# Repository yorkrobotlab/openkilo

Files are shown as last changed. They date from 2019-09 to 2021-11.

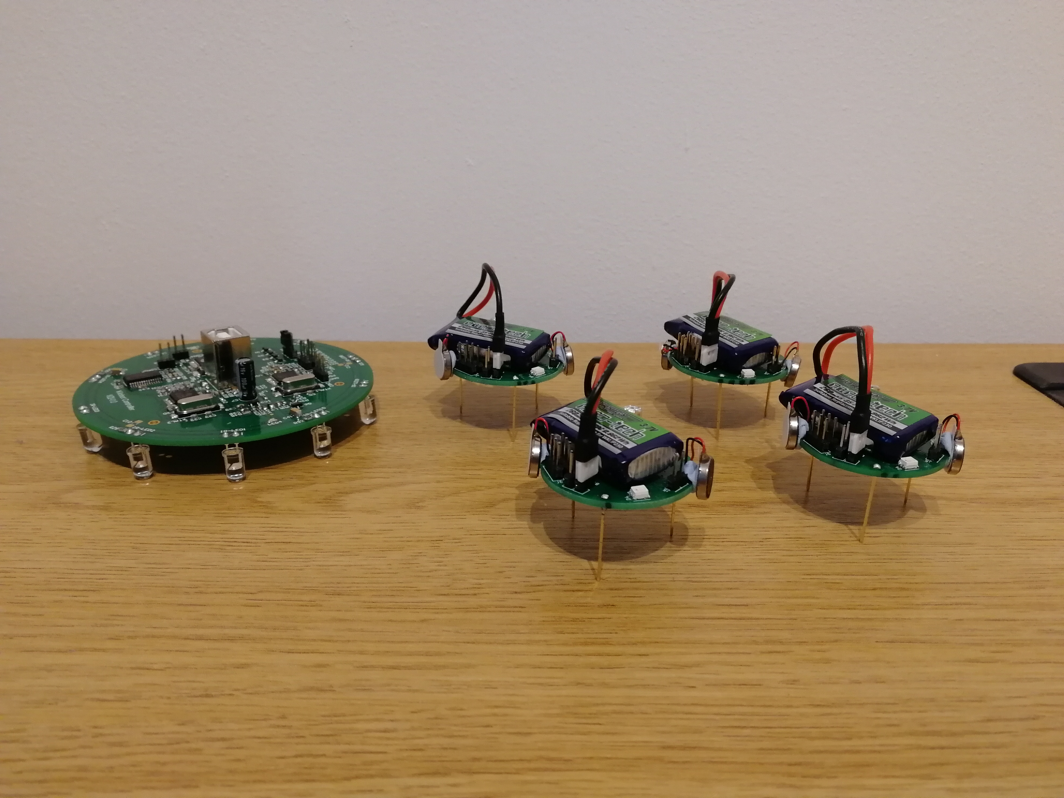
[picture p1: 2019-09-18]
Photos and Video/with_OHC.jpg

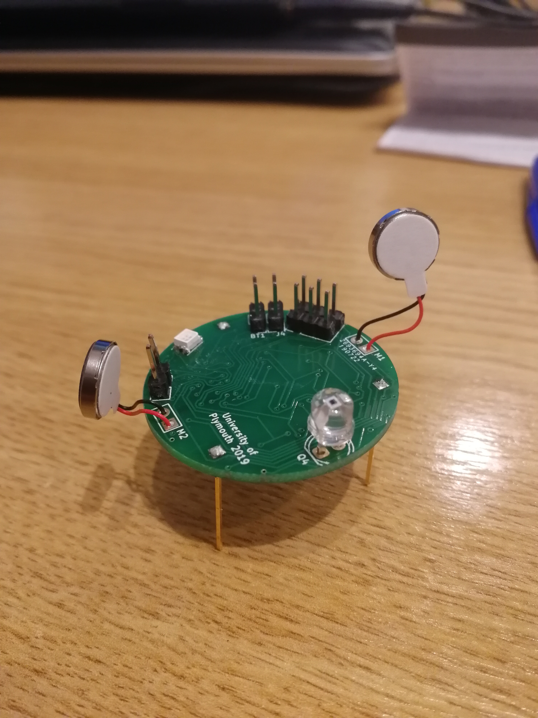
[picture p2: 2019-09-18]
Photos and Video/without_battery.jpg

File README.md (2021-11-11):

# OpenKilo

This repository contains resources related to the OpenKilo Kilobot revision, which was designed to aid repair and extensibility of the Kilobot platform.

This project was possible due to the material made open-source by other institutions, most importantly [Harvard University](https://ssr.seas.harvard.edu/kilobots) and [Western Carolina University](https://kilobot.wcu.edu/).

## Contents

* [Hardware Design](Hardware%20Design/) - KiCad project and exported Gerber files used to produce this version of the Kilobot
* [Documentation](Documentation/) - hardware schematic (produced from Harvard and WCU designs), assembly and programming guides, and bill of materials
* [Photos and Video](Photos%20and%20Video/) - showing the completed robots and their usage

## Requirements

Our Overhead Controller (OHC) was built to a design by Western Carolina University (WCU). Their detailed guide was also used for the programming and control of both the OHC and Kilobots. For more details, refer to their material at https://kilobot.wcu.edu/.

In particular:

* OHC Gerber files
* Software folder including Kilobot and OHC firmware
* [KiloGUI](https://github.com/acornejo/kilogui), GUI application for Kilobot control
* [Maker: A Kilobot Swarm](https://www.asee.org/public/conferences/64/papers/15441/view)

### Editing the PCB
[KiCad EDA](http://kicad.org/) is a free open-source electronic CAD suite which was used to create the OpenKilo design. KiCad is required in order to make changes to the design, but the exported Gerber files are also available for use directly.

The included Kilobot.lib is required for certain symbols and footprints, and must be added to the KiCad project using the process described [here](https://forum.kicad.info/t/library-management-in-kicad-version-5/14636).

[freeRouting](https://freerouting.org/) was used in conjunction with KiCad to carry out automatic PCB routing for the current design.

## Build Process
1. Purchase all PCBs and required components using BOMs included here. For the OHC PCB, use WCU Gerber files.

2. Following the guide in [Maker: A Kilobot Swarm](https://www.asee.org/public/conferences/64/papers/15441/view), install the required software before assembling the OHC and programming its firmware.

3. Assemble the OpenKilo hardware using the included assembly diagram and checklists.

4. Continuing with the WCU guide, program Kilobot firmware using a 2x3 header cable. Connection details are given in [Programming Reference.pdf](Documentation/Programming%20Reference.pdf).

5. Install KiloGUI and use the OHC to program a benchmark test onto the OpenKilo robots. These tests can be found in the WCU materials as well as at [Kilobotics](https://www.kilobotics.com/labs) where details of their functions are available.

## Author
The main OpenKilo design and prototyping was completed by Jamie Trump while a postgraduate student in the [School of Engineering, Computing and Mathematics](https://www.plymouth.ac.uk/schools/school-of-engineering-computing-and-mathematics) at the [University of Plymouth](https://www.plymouth.ac.uk/).

His original project repository can be found at [github.com/jamie-trump/Plymouth-Kilobot-2019](https://github.com/jamie-trump/Plymouth-Kilobot-2019).

This work is licensed under a [Creative Commons Attribution-NonCommercial-ShareAlike 4.0 International License](http://creativecommons.org/licenses/by-nc-sa/4.0/).

## Links

### Information and Publications
* [Kilobot @ WCU](https://kilobot.wcu.edu/)
* [Maker: A Kilobot Swarm](https://www.asee.org/public/conferences/64/papers/15441/view)
* [Kilobotics Labs](https://www.kilobotics.com/labs)

### Software
* [KiloGUI](https://github.com/acornejo/kilogui)
* [KiCad EDA](http://kicad.org/)
* [freeRouting](https://freerouting.org/)

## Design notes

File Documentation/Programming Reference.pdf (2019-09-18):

## Kilobot firmware programming connections

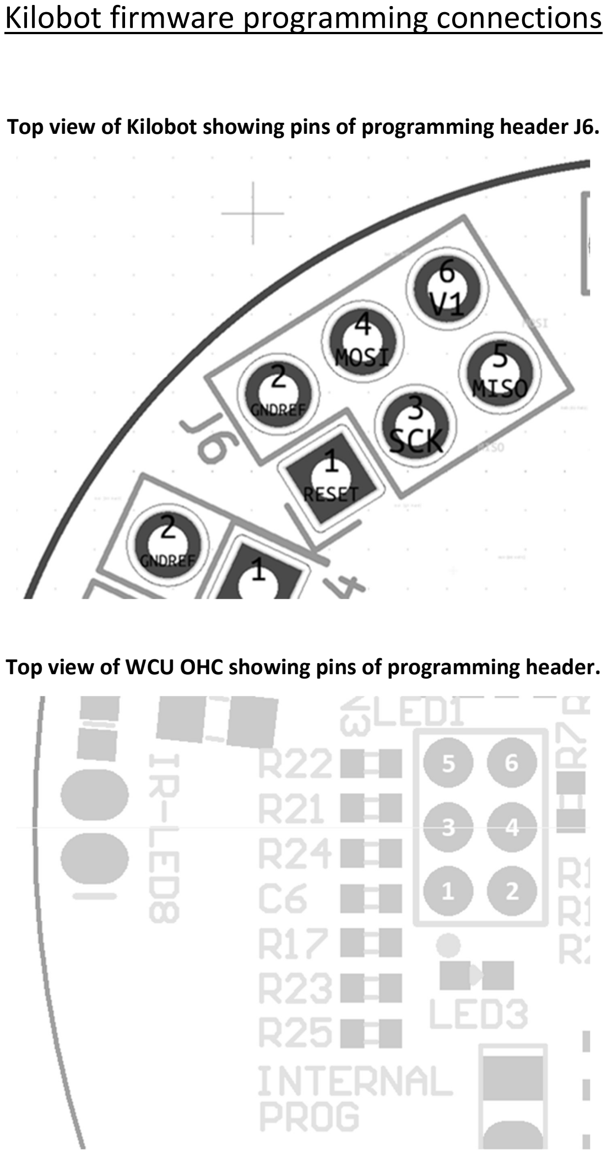
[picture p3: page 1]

Top view of Kilobot showing pins of programming header J6.

Top view of WCU OHC showing pins of programming header.

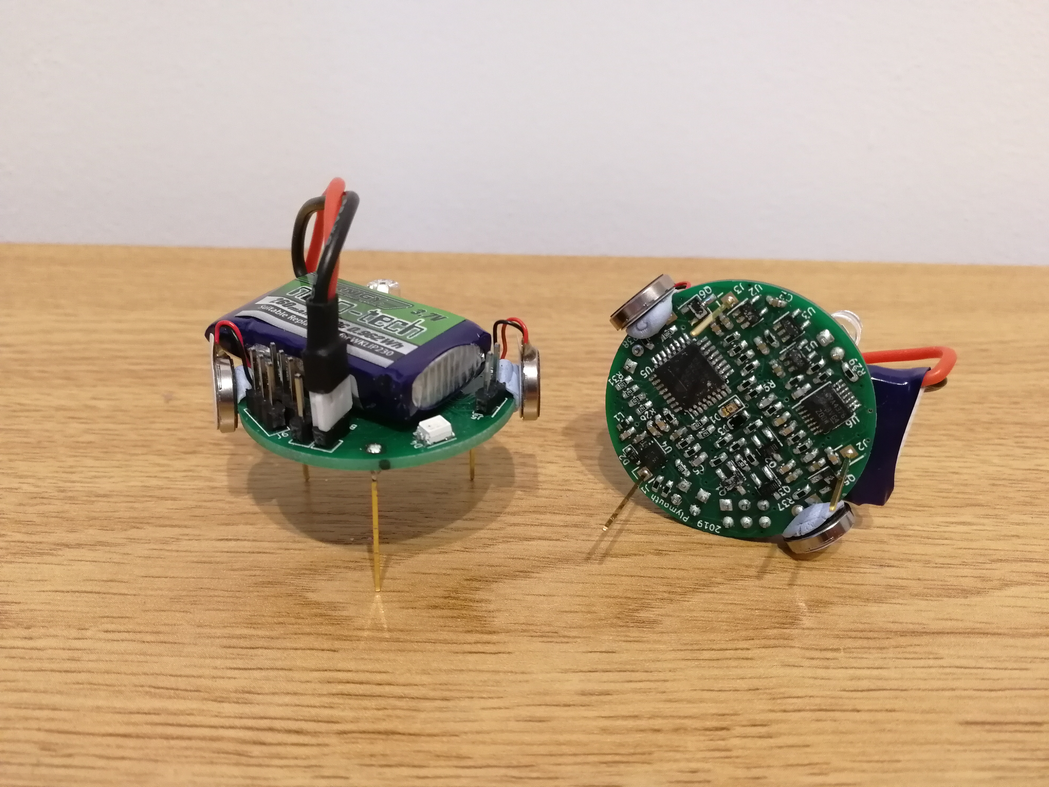
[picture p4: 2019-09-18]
Photos and Video/kilobots1.jpg

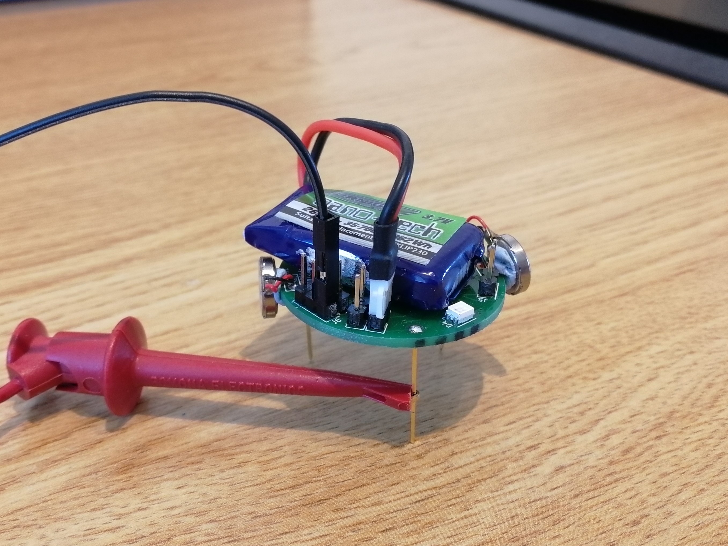
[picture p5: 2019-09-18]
Photos and Video/charging.jpg

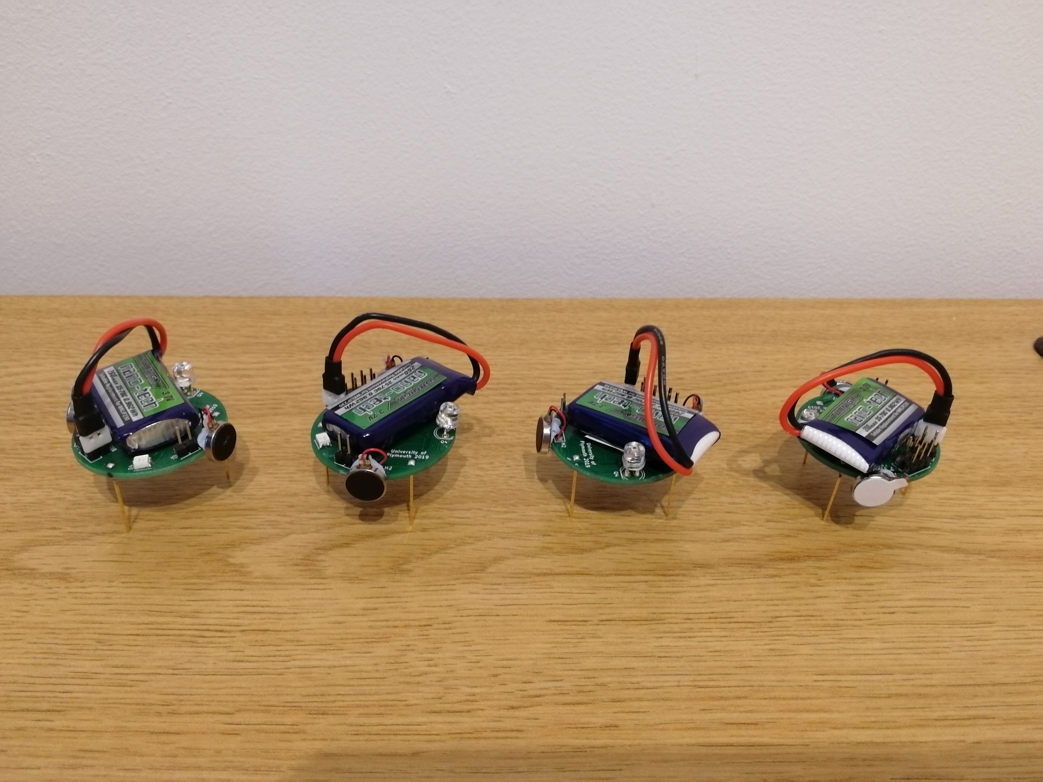
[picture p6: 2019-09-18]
Photos and Video/kilobots2.jpg

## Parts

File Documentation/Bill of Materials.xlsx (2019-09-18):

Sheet: 5x Kilobots
MyRef | Ordered Qty | Description | Supplier | Order Code | Price each (@qty), £ ex vat | Total (@qty), £ ex vat
1 | 50 | CAP CER 2.2UF 6.3V Y5V 0603 | Farnell | 2627450 | 0.0985 | 4.925
2 | 25 | CAP CER 10000PF 25V 10% X7R 0603 | Farnell | 1856354 | 0.0337 | 0.843
3 | 10 | CAP CER 0.1UF 16V 10% X7R 0603 | Farnell | 1327679 | 0.1020 | 1.020
4 | 10 | CAP CER 1000PF 50V 5% NP0 0603 | Farnell | 8819920 | 0.0700 | 0.700
5 | 5 | CAP CER 10000PF 25V 5% C0G 0603 | Digikey | 1276-2172-1-ND | 0.2700 | 1.350
6 | 10 | CAP CER 68PF 50V 5% C0G 0603 | Farnell | 1907295 | 0.1410 | 1.410
7 | 5 | IC CHARGER LI-ION USB/AC 10WSON | Digikey | LM3658SD-A/NOPBCT-ND | 1.0600 | 5.300
8 | 5 | DIODE SCHOTTKY 30V 100MA 0603 | Digikey | 641-1282-1-ND | 0.3500 | 1.750
9 | 10 | FIXED IND 10UH 50MA 900 MOHM | Farnell | 2840127 | 0.1080 | 1.080
10 | 5 | IC OPAMP GP 5.5MHZ RRO 14TSSOP | Digikey | 296-22565-1-ND | 2.6500 | 13.250
11 | 10 | RES SMD 0.82 OHM 1% 1/10W 0603 | Farnell | 1717771 | 0.0717 | 0.717
12 | 10 | RES SMD 1.18K OHM 1% 1/10W 0603 | Farnell | 2303149 | 0.0374 | 0.374
13 | 5 | RES SMD 1.47K OHM 1% 1/10W 0603 | Digikey | P1.47KHCT-ND | 0.0800 | 0.400
14 | 15 | RES SMD 1.6K OHM 5% 1/10W 0603 | Digikey | P1.6KGCT-ND | 0.0340 | 0.510
15 | 5 | RES SMD 1.62K OHM 1% 1/10W 0603 | Digikey | P1.62KHCT-ND | 0.0800 | 0.400
16 | 20 | RES SMD 10K OHM 1% 1/10W 0603 | Farnell | 2303192 | 0.0374 | 0.748
17 | 10 | RES SMD 10 OHM 1% 1/10W 0603 | Farnell | 2302958 | 0.0374 | 0.374
18 | 10 | RES SMD 11K OHM 1% 1/10W 0603 | Farnell | 2059409 | 0.0374 | 0.374
19 | 10 | RES SMD 154 OHM 1% 1/10W 0603 | Farnell | 2303077 | 0.0329 | 0.329
20 | 10 | RES SMD 2M OHM 5% 1/10W 0603 | Farnell | 2059687 | 0.0227 | 0.227
21 | 10 | RES SMD 2.26K OHM 1% 1/10W 0603 | Farnell | 2303167 | 0.0374 | 0.374
22 | 5 | RES SMD 2.37K OHM 1% 1/10W 0603 | Digikey | P2.37KHCT-ND | 0.0800 | 0.400
23 | 10 | RES SMD 20K OHM 1% 1/10W 0603 | Farnell | 2059432 | 0.0374 | 0.374
24 | 10 | RES SMD 200 OHM 1% 1/10W 0603 | Farnell | 2059293 | 0.0374 | 0.374
25 | 20 | RES SMD 25.5K OHM 1% 1/10W 0603 | Digikey | P25.5KHCT-ND | 0.0510 | 1.020
26 | 10 | RES SMD 280K OHM 1% 1/10W 0603 | Farnell | 2059515 | 0.0374 | 0.374
27 | 10 | RES SMD 301 OHM 1% 1/10W 0603 | Farnell | 2059304 | 0.0374 | 0.374
28 | 10 | RES SMD 4.87K OHM 1% 1/10W 0603 | Farnell | 2303624 | 0.0374 | 0.374
29 | 10 | RES SMD 499 OHM 1% 1/10W 0603 | Farnell | 2059311 | 0.0374 | 0.374
30 | 10 | RES SMD 4.99K OHM 1% 1/10W 0603 | Farnell | 2059377 | 0.0374 | 0.374
31 | 10 | RES SMD 5.62K OHM 1% 1/10W 0603 | Farnell | 2059384 | 0.0374 | 0.374
32 | 10 | RES SMD 549K OHM 1% 1/10W 0603 | Farnell | 2059522 | 0.0294 | 0.294
33 | 5 | RES SMD 604K OHM 1% 1/10W 0603 | Digikey | P604KHCT-ND | 0.0800 | 0.400
34 | 20 | RES SMD 820 OHM 5% 1/10W 0603 | Farnell | 2059598 | 0.0248 | 0.496
35 | 10 | RES SMD 806 OHM 1% 1/10W 0603 | Farnell | 2059324 | 0.0374 | 0.374
36 | 10 | RES SMD 9.76K OHM 1% 1/10W 0603 | Farnell | 2303191 | 0.0374 | 0.374
38 | 5 | IC REG LDO 3V 0.2A SOT25 | Farnell | 1454271 | 0.3350 | 1.675
39 | 10 | IC REG LDO 3V 0.7A SOT25 | Digikey | 893-1074-1-ND | 0.6050 | 6.050
40 | 5 | LED RGB 4PLCC | Digikey | VAOS-SP4RGB4CT-ND | 1.6400 | 8.200
41 | 10 | TRANS NPN 20V 0.5A SOT-346 | Digikey | 2SD2114KT146WCT-ND | 0.2720 | 2.720
42 | 15 | TRANS NPN 50V 0.5A SOT-23 | Farnell | 1680156 | 0.2640 | 3.960
43 | 5 | IC MCU 8BIT 32KB FLASH 32VQFN | Farnell | 1715486 | 1.4400 | 7.200
44 | 10 | Shaftless Vibration Motor 10x2.0mm | Rapid | 75-0416 | 0.9110 | 9.110
45 | 1 | 5Pack - Lipo battery 260mAh | Hobbyking | 9067000289-0 | 3.9400 | 3.940
46 | 50 | SHUNT JUMPER .1" BLACK GOLD | Farnell | 2834671 | 0.0350 | 1.750
47 | 1 | CONN HEADER 50POS .100" SGL GOLD | Farnell | 2856767 | 3.9100 | 3.910
49 | 5 | EMITTER IR 940NM 100MA 0805 | Digikey | VSMB1940X01CT-ND | 0.8200 | 4.100
50 | 5 | PHOTODIODE PIN 950NM 0805 | Digikey | TEMD7100X01CT-ND | 0.8600 | 4.300
51 | 2 | 20 Positions Header, Unshrouded, 0.100" | Digikey | S1011EC-20-ND | 0.3900 | 0.780
53 | 5 | AMBIENT LIGHT SENSOR 5MM 570NM | Farnell | 1497676 | 0.6410 | 3.205
 |  |  |  |  | Total | £103.70

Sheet: 1x OHC (WCU)
MyRef | Ordered Qty | Description | Supplier | Order Code | Price each (@qty), £ ex vat | Total (@qty), £ ex vat
101 | 15 | CAP CER 0.1UF 25V 10% X7R 0603 (*) | Digikey | 478-7018-1-ND | 0.1000 | 1.5000
102 | 10 | CAP CER 1UF 10V 10% X5R 0603 (*) | Digikey | 490-1543-1-ND | 0.0980 | 0.9800
103 | 20 | CAP CER 22PF 50V 5% C0G 0603 (*) | Farnell | 1907288 | 0.1420 | 2.8400
104 | 1 | CAP ALUM 100UF 16V 20% RADIAL | Digikey | 493-1040-ND | 0.2000 | 0.2000
106 | 3 | CAP CER 47UF 6.3V 20% X5R 1206 | Digikey | 490-3907-1-ND | 0.6100 | 1.8300
109 | 1 | IC MCU 8BIT 32KB FLASH 32TQFP | Farnell | 2443176 | 1.4500 | 1.4500
110 | 1 | IC 2/3-PORT USB HUB 32-LQFP | Digikey | 296-27129-6-ND | 2.6100 | 2.6100
111 | 1 | IC REG LDO 3.3V 0.15A SOT23-5 | Farnell | 2851612 | 0.0273 | 0.0273
112 | 1 | IC USB FS SERIAL UART 28-SSOP | Farnell | 1146032 | 3.4300 | 3.4300
113 | 1 | IC MCU 8BIT 16KB FLASH 32TQFP | Farnell | 1455073 | 2.0200 | 2.0200
114 | 10 | EMITTER IR 870NM 100MA RADIAL (*) | Digikey | 751-1208-ND | 0.7390 | 7.3900
115 | 3 | FERRITE CHIP 1000 OHM 1.5A 0805 | Digikey | 445-5223-1-ND | 0.0900 | 0.2700
116 | 10 | LED 572NM YW/GN WH/DIFF 0603 SMD | Farnell | 2687485 | 0.0206 | 0.2060
117 | 2 | LED BLUE HIGH BRIGHT ESS SMD | Digikey | 1080-1581-1-ND | 0.2800 | 0.5600
118 | 5 | MOSFET N-CH 50V 220MA SOT-23-3 | Farnell | 2453386 | 0.2130 | 1.0650
119 | 1 | MOSFET N-CH 20V 2.1A SOT23-3 | Farnell | 1426253 | 0.4100 | 0.4100
120 | 10 | RES SMD 47K OHM 1% 1/10W 0603 | Farnell | 2303213 | 0.0374 | 0.3740
121 | 10 | RES SMD 2K OHM 5% 1/10W 0603 | Farnell | 2059609 | 0.0248 | 0.2480
122 | 20 | RES SMD 1K OHM 1% 1/10W 0603 (**) | Farnell | 2303145 | 0.0374 | 0.7480
123 | 10 | RES SMD 300 OHM 5% 1/10W 0603 | Farnell | 2059586 | 0.0218 | 0.2180
124 | 10 | RES SMD 28K OHM 1% 1/10W 0603 | Farnell | 2059449 | 0.0374 | 0.3740
125 | 10 | RES SMD 100 OHM 1% 1/10W 0603 | Farnell | 2303059 | 0.0374 | 0.3740
126 | 10 | RES SMD 1 OHM 5% 1/8W 0805 (*) | Farnell | 2333534 | 0.0233 | 0.2330
127 | 10 | RES SMD 1.5K OHM 5% 1/10W 0603 | Farnell | 2059606 | 0.0246 | 0.2460
128 | 10 | RES SMD 27 OHM 5% 1/10W 0603 (**) | Farnell | 2059559 | 0.0246 | 0.2460
129 | 10 | RES SMD 0.0 OHM JUMPER 1/10W | Farnell | 1469739 | 0.0149 | 0.1490
130 | 10 | RES SMD 15K OHM 5% 1/10W 0603 | Farnell | 2059633 | 0.0246 | 0.2460
131 | 1 | CONN USB JACK TYPE B VERT STR | Digikey | 151-1083-ND | 1.2100 | 1.2100
132 | 1 | CRYSTAL 8MHZ 18PF SMD | Farnell | 2467757 | 0.2110 | 0.2110
133 | 1 | CRYSTAL 6MHZ 20PF SMD | Digikey | XC1000CT-ND | 0.3900 | 0.3900
134 | 1 | CRYSTAL 16MHZ 18PF SMD | Farnell | 2467721 | 0.2090 | 0.2090
 |  |  |  |  | Total | £32.26

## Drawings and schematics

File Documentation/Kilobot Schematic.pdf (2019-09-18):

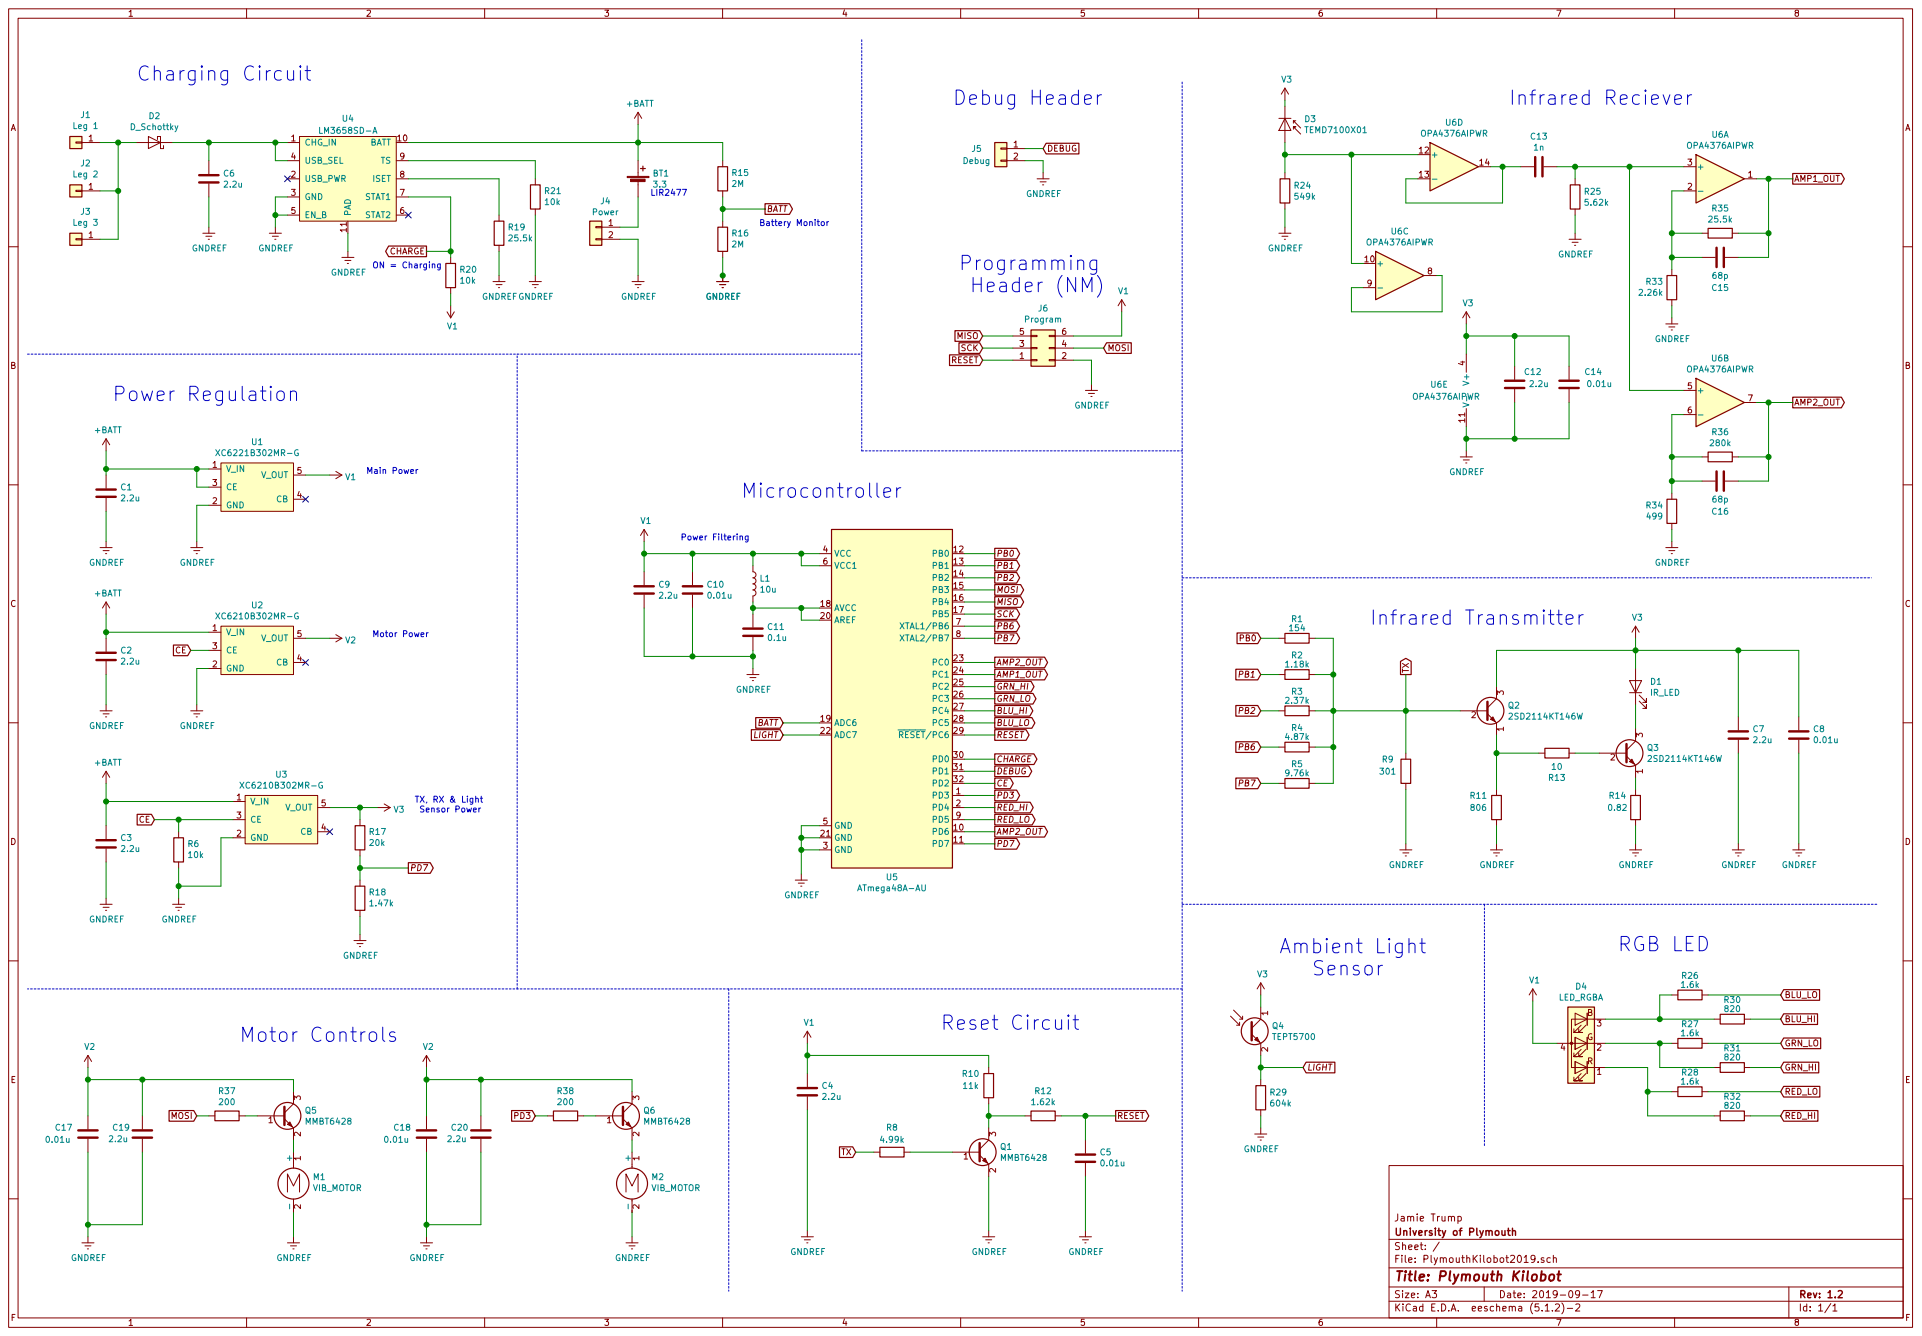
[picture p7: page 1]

AMP2_OUT Debug Header Motor PowerTX, RX & Light

MOSI RESET SCK MISO

Jamie Trump
File: PlymouthKilobot2019.sch Sheet: / University of Plymouth

Id: 1/1 Title: Plymouth Kilobot

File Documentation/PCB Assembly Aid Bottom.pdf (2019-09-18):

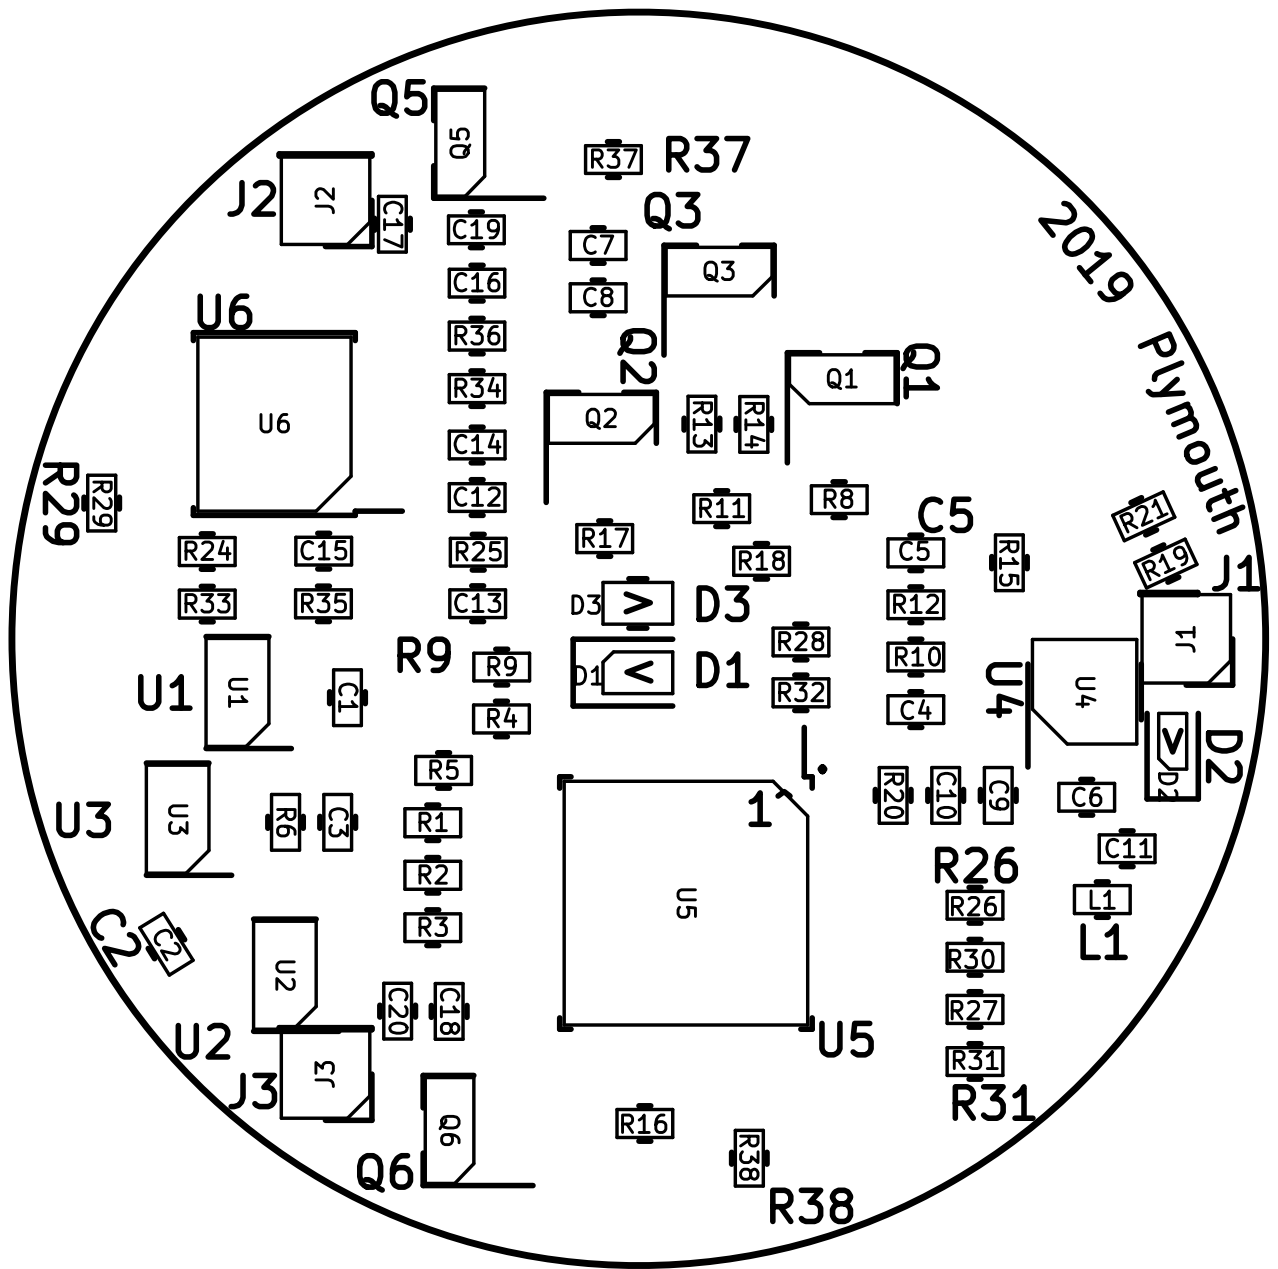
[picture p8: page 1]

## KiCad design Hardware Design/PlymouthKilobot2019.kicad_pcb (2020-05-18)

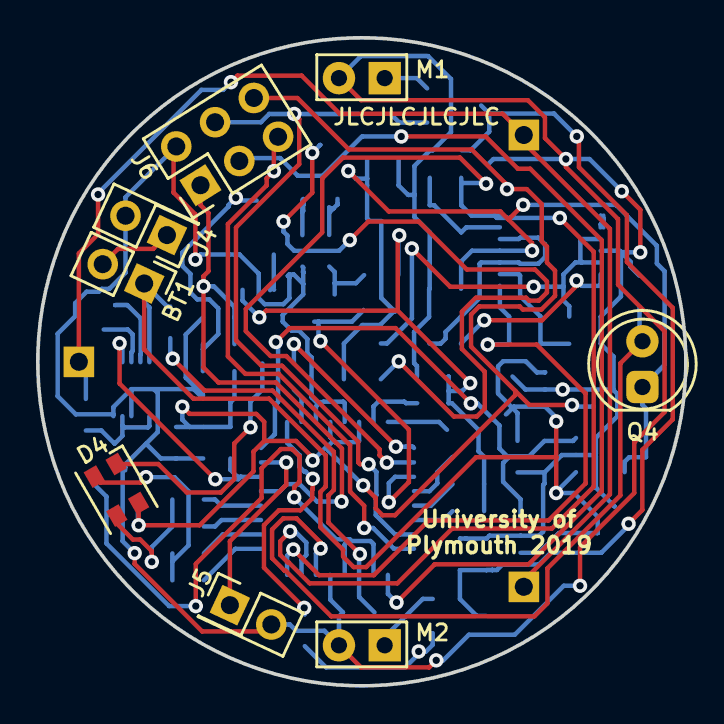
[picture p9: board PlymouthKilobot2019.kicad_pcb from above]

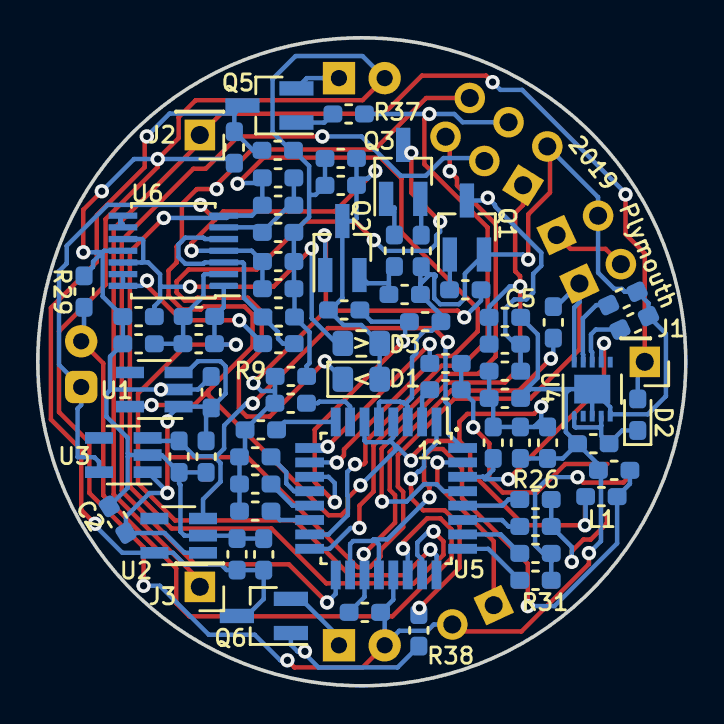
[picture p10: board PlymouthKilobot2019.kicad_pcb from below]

Board: 2 copper layers, 36.0 x 36.0 mm, 81 parts (73 on the bottom side), 55 nets.

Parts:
BT1: 3.3; PinHeader_1x02_P2.54mm_Vertical
C1, C2, C3, C4, C6, C7, C9, C12, C19, C20: 2.2u; C_0603_1608Metric_Pad1.05x0.95mm_HandSolder
C5, C8, C10, C14, C17, C18: 0.01u; C_0603_1608Metric_Pad1.05x0.95mm_HandSolder
C11: 0.1u; C_0603_1608Metric_Pad1.05x0.95mm_HandSolder
C13: 1n; C_0603_1608Metric_Pad1.05x0.95mm_HandSolder
C15, C16: 68p; C_0603_1608Metric_Pad1.05x0.95mm_HandSolder
D1: IR_LED; LED_0805_2012Metric_Pad1.15x1.40mm_HandSolder
D2: D_Schottky; D_0603_1608Metric_Pad1.05x0.95mm_HandSolder
D3: TEMD7100X01; R_0805_2012Metric_Pad1.15x1.40mm_HandSolder
D4: LED_RGBA; LED_Cree-PLCC4_3.2x2.8mm_CCW
J1: Leg 1; PinHeader_1x01_P2.54mm_Vertical
J2: Leg 2; PinHeader_1x01_P2.54mm_Vertical
J3: Leg 3; PinHeader_1x01_P2.54mm_Vertical
J4: Power; PinHeader_2x01_P2.54mm_Vertical
J5: Debug; PinHeader_2x01_P2.54mm_Vertical
J6: Program; PinHeader_2x03_P2.54mm_Vertical
L1: 10u; L_0603_1608Metric_Pad1.05x0.95mm_HandSolder
M1, M2: VIB_MOTOR; Vibration_Motor_10x2mm_Vert_noBody
Q1, Q5, Q6: MMBT6428; SOT-23_Handsoldering
Q2, Q3: 2SD2114KT146W; SOT-23_Handsoldering__pins_changed
Q4: TEPT5700; LED_D5.0mm_Clear
R1: 154; R_0603_1608Metric_Pad1.05x0.95mm_HandSolder
R2: 1.18k; R_0603_1608Metric_Pad1.05x0.95mm_HandSolder
R3: 2.37k; R_0603_1608Metric_Pad1.05x0.95mm_HandSolder
R4: 4.87k; R_0603_1608Metric_Pad1.05x0.95mm_HandSolder
R5: 9.76k; R_0603_1608Metric_Pad1.05x0.95mm_HandSolder
R6, R20, R21: 10k; R_0603_1608Metric_Pad1.05x0.95mm_HandSolder
R8: 4.99k; R_0603_1608Metric_Pad1.05x0.95mm_HandSolder
R9: 301; R_0603_1608Metric_Pad1.05x0.95mm_HandSolder
R10: 11k; R_0603_1608Metric_Pad1.05x0.95mm_HandSolder
R11: 806; R_0603_1608Metric_Pad1.05x0.95mm_HandSolder
R12: 1.62k; R_0603_1608Metric_Pad1.05x0.95mm_HandSolder
R13: 10; R_0603_1608Metric_Pad1.05x0.95mm_HandSolder
R14: 0.82; R_0603_1608Metric_Pad1.05x0.95mm_HandSolder
R15, R16: 2M; R_0603_1608Metric_Pad1.05x0.95mm_HandSolder
R17: 20k; R_0603_1608Metric_Pad1.05x0.95mm_HandSolder
R18: 1.47k; R_0603_1608Metric_Pad1.05x0.95mm_HandSolder
R19, R35: 25.5k; R_0603_1608Metric_Pad1.05x0.95mm_HandSolder
R24: 549k; R_0603_1608Metric_Pad1.05x0.95mm_HandSolder
R25: 5.62k; R_0603_1608Metric_Pad1.05x0.95mm_HandSolder
R26, R27, R28: 1.6k; R_0603_1608Metric_Pad1.05x0.95mm_HandSolder
R29: 604k; R_0603_1608Metric_Pad1.05x0.95mm_HandSolder
R30, R31, R32: 820; R_0603_1608Metric_Pad1.05x0.95mm_HandSolder
R33: 2.26k; R_0603_1608Metric_Pad1.05x0.95mm_HandSolder
R34: 499; R_0603_1608Metric_Pad1.05x0.95mm_HandSolder
R36: 280k; R_0603_1608Metric_Pad1.05x0.95mm_HandSolder
R37, R38: 200; R_0603_1608Metric_Pad1.05x0.95mm_HandSolder
U1: XC6221B302MR-G; SOT-23-5_HandSoldering
U2, U3: XC6210B302MR-G; SOT-23-5_HandSoldering
U4: LM3658SD-A; WSON-10-1EP_3x3mm_P0.5mm_EP0.6x2.5mm
U5: ATmega48A-AU; TQFP-32_7x7mm_P0.8mm
U6: OPA4376AIPWR; TSSOP-14_4.4x5mm_P0.65mm_altered

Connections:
+BATT: BT1.1, C1.2, C2.2, C3.2, R15.2, U1.1, U1.3, U2.1, U3.1, U4.10
AMP1_OUT: C15.1, R35.1, U5.24, U6.1
AMP2_OUT: C16.1, R36.1, U5.10, U5.23, U6.7
BATT: R15.1, R16.2, U5.19
BLU_HI: R30.1, U5.27
BLU_LO: R26.1, U5.28
CE: R6.2, U2.3, U3.3, U5.32
CHARGE: R20.2, U4.7, U5.30
DEBUG: J5.1, U5.31
GNDREF: C1.1, C2.1, C3.1, C4.1, C5.1, C6.2, C7.1, C8.1, C9.2, C10.2, C11.2, C12.1, C14.1, C17.1, C18.1, C19.1, C20.1, J4.2, J5.2, J6.2, M1.2, M2.2, Q1.2, R6.1, R9.2, R11.2, R14.2, R16.1, R18.1, R19.1, R21.1, R24.2, R25.2, R29.2, R33.1, R34.1, U1.2, U2.2, U3.2, U4.3, U4.5, U4.11, U5.3, U5.5, U5.21, U6.11
GRN_HI: R31.1, U5.25
GRN_LO: R27.1, U5.26
LIGHT: Q4.2, R29.1, U5.22
MISO: J6.5, U5.16
MOSI: J6.4, R37.1, U5.15
unnamed: BT1.2, J4.1
unnamed: C6.1, D2.1, U4.1, U4.4
unnamed: C11.1, L1.2, U5.18, U5.20
unnamed: C13.1, R25.1, U6.3, U6.5
unnamed: C13.2, U6.13, U6.14
unnamed: C15.2, R33.2, R35.2, U6.2
unnamed: C16.2, R34.2, R36.2, U6.6
unnamed: D1.1, Q3.3
unnamed: D2.2, J1.1, J2.1, J3.1
unnamed: D3.2, R24.1, U6.10, U6.12
unnamed: D4.1, R28.2, R32.2
unnamed: D4.2, R27.2, R31.2
unnamed: D4.3, R26.2, R30.2
unnamed: M1.1, Q5.2
unnamed: M2.1, Q6.2
unnamed: Q1.1, R8.1
unnamed: Q1.3, R10.2, R12.2
unnamed: Q2.1, R11.1, R13.1
unnamed: Q3.1, R14.1
unnamed: Q3.2, R13.2
unnamed: Q5.1, R37.2
unnamed: Q6.1, R38.2
unnamed: R19.2, U4.8
unnamed: R21.2, U4.9
unnamed: U6.8, U6.9
PB0: R1.2, U5.12
PB1: R2.2, U5.13
PB2: R3.2, U5.14
PB6: R4.2, U5.7
PB7: R5.2, U5.8
PD3: R38.1, U5.1
PD7: R17.1, R18.2, U5.11
RED_HI: R32.1, U5.2
RED_LO: R28.1, U5.9
RESET: C5.2, J6.1, R12.1, U5.29
SCK: J6.3, U5.17
TX: Q2.2, R1.1, R2.1, R3.1, R4.1, R5.1, R8.2, R9.1
V1: C4.2, C9.1, C10.1, D4.4, J6.6, L1.1, R10.1, R20.1, U1.5, U5.4, U5.6
V2: C17.2, C18.2, C19.2, C20.2, Q5.3, Q6.3, U2.5
V3: C7.2, C8.2, C12.2, C14.2, D1.2, D3.1, Q2.3, Q4.1, R17.2, U3.5, U6.4

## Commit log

2020-05-18 Added KiCad hardware design files and Gerber files
    Expanded from the zip files, which have now been removed.
    [Kilobot v2-0-B_Cu.gbr, Kilobot v2-0-B_Mask.gbr, Kilobot v2-0-B_SilkS.gbr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]
2021-11-10 Update README.md
    https://forum.kicad.info/t/warning-avoid-all-links-to-kicad-pcb-org-use-kicad-org/31521
